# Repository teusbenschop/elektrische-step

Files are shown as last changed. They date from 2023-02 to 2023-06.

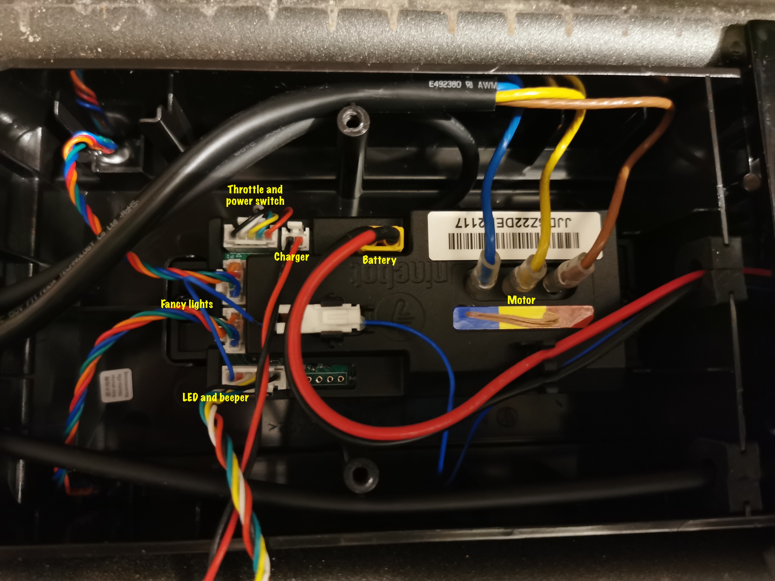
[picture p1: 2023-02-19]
Remarks/Controller-wiring.jpg

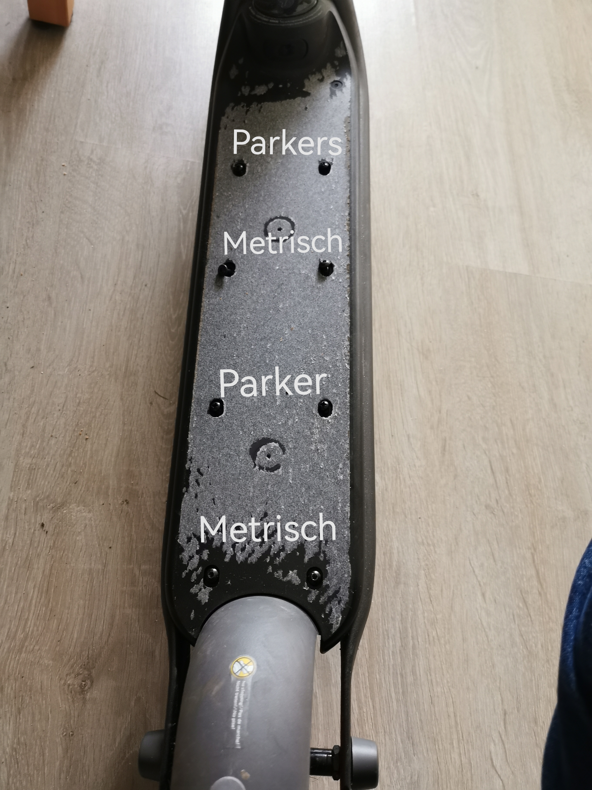
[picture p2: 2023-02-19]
Remarks/Zing C20 foot rest screws.jpg

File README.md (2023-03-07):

# Legale elektrische step

Ideeën en schemas en code voor een elektrische step die legaal is binnen Nederland.

Op de [website van de rijksoverheid.nl staat waaraan een elektrische step moet voldoen om legaal de openbare weg op te kunnen](https://www.rijksoverheid.nl/onderwerpen/voertuigen-op-de-weg/e-step-met-trapondersteuning).

Dit is een samenvatting van het artikel (gecontroleerd maart 2023):

---

Wat is een e-step met trapondersteuning? 
* U stept zelf op deze e-step. 
* Door de hulpmotor gaat u harder vooruit. 
* Maar niet harder dan 25 kilometer per uur.
* De hulpmotor heeft een vermogen van maximaal 250 Watt.

Regels voor gebruik e-step met trapondersteuning.
Voor deze e-step gelden dezelfde regels als voor een elektrische fiets. U hoeft bijvoorbeeld geen rijbewijs te hebben.

Uitrusting die een e-step met trapondersteuning moet hebben:
Een e-step met trapondersteuning heeft:
* een stuur;
* verlichting; 
* rode en witte/gele reflectoren.

Let op! Sommige e-steps hebben een gashendel. Deze werkt niet. Werkt de gashendel wel? Dan is uw e-step een bijzondere bromfiets.

---

Einde samenvatting.

Op de [website van de politieacademie.nl staat ongeveer hetzelfde](https://webapps.politieacademie.nl/bijzondere-bromfiets/53484).

Om een bestaande elektrische step legaal te maken is er het idee om de step te voorzien van detectoren die detecteren als de bestuurder van de step een stepbeweging maakt door met het been af te zetten tijdens het steppen. Dit idee is vorm te geven door lichtbronnen te monteren aan de voetenplank van de step, plus detectoren om de reflectie van dit licht op de voet, die afzet, te detecteren. Dit patroon van reflectie kan dan in een computertje ingevoerd worden, en dat computertje kan dan de motor van de step uitschakelen als er geen beweging van de bestuurder gedetecteerd wordt gedurende een aantal seconden.

De lichtbronnen en lichtdetectoren worden dan gemonteerd op de juiste plaats van de voetenplank waar die het beste de beweging van het been kan detecteren als de bestuurder met de voet afzet.

Als de step nog een gashendel heeft, dan mag die gashendel niet werken.
De meest eenvoudige oplossing is om de gashendel gewoon te verwijderen.
Daarnaast is het als optie mogelijk om een remhendel van bijvoorbeeld de Xiaomi Mi M365 te monteren op de plaats waar de gashendel zat. Die remhendel kan dan fungeren als dodemansknop. Zodra de dodemanshendel ingeknepen wordt, dan wordt de motor toegelaten eventueel aan te gaan als aan alle voorwaarden wordt voldaan. Zodra de dodemanshendel losgelaten wordt, dan schakelt de motor in alle gevallen direct uit.

Hier in deze repository staan een aantal bestanden die de elektonische schakeling weergeven, plus de programmatuur, dat bovenstaand idee vormgeeft.

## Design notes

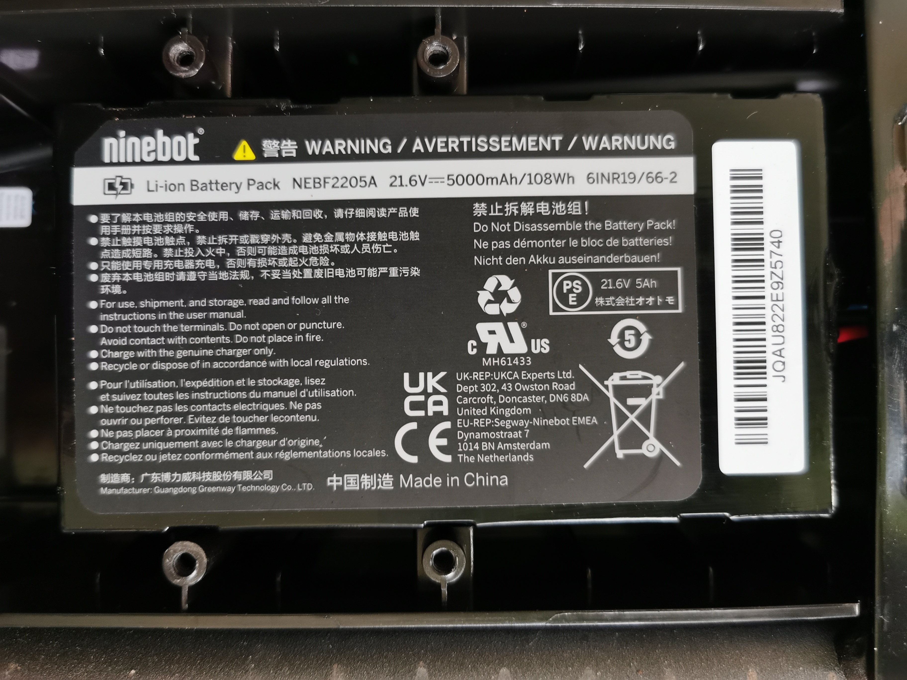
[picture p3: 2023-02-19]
Remarks/Zing-C20-battery.jpg

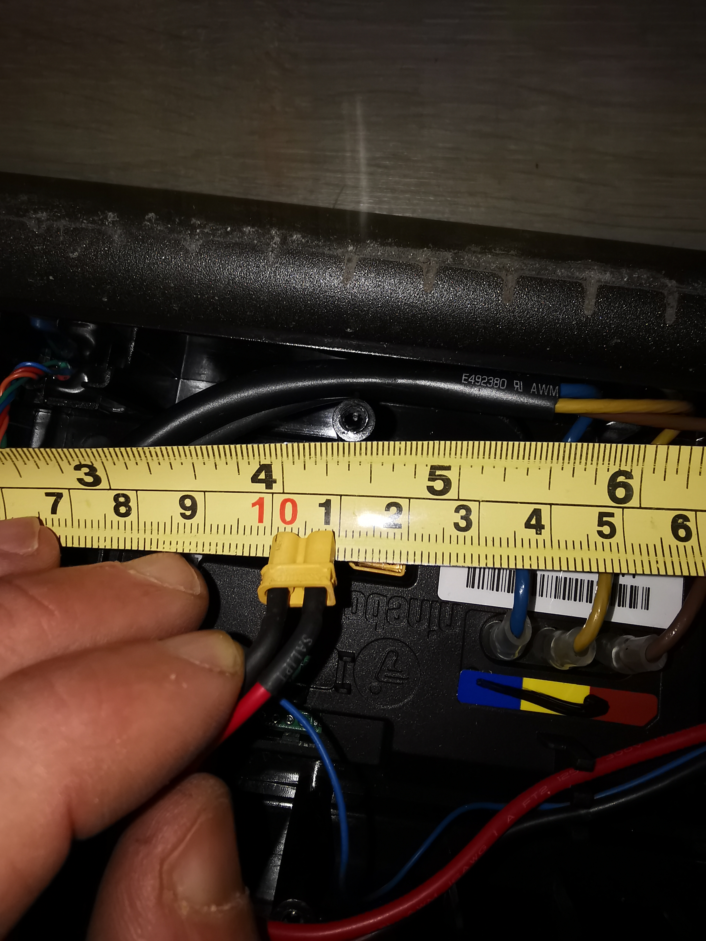
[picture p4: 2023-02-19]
Remarks/XT30-battery-connector.jpg

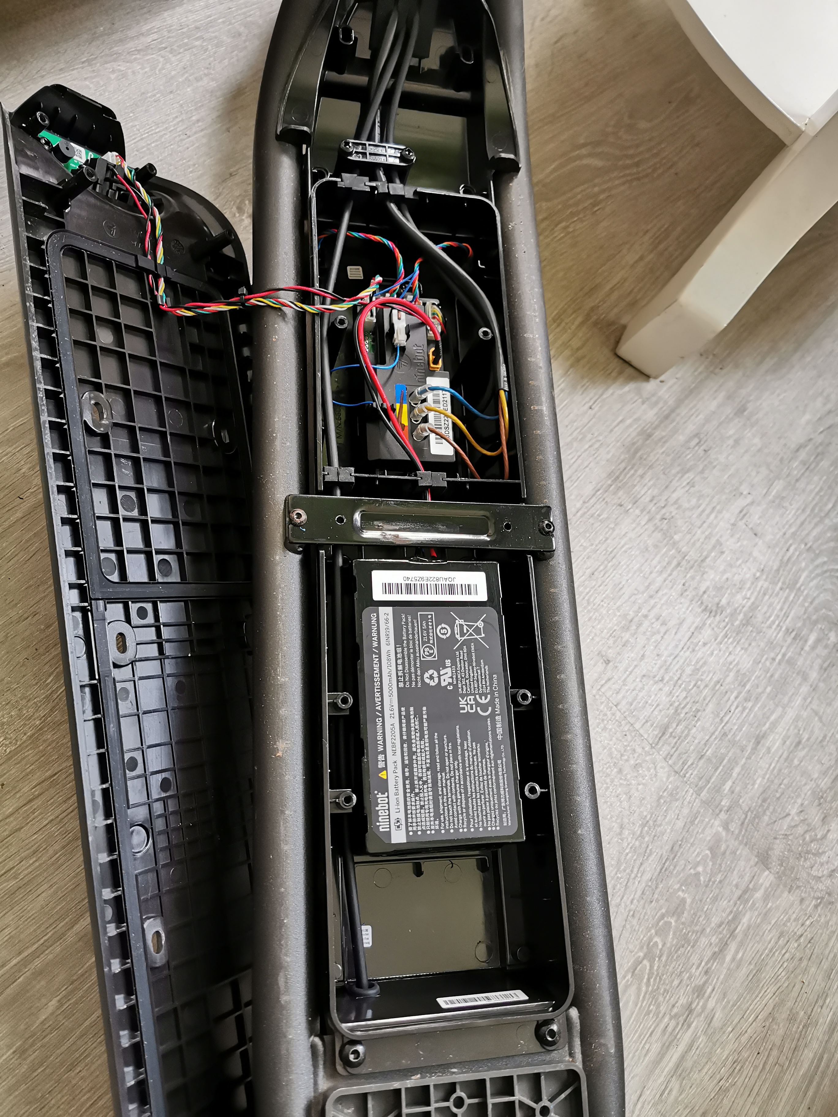
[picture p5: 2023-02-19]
Remarks/Zing C20 bottom box.jpg

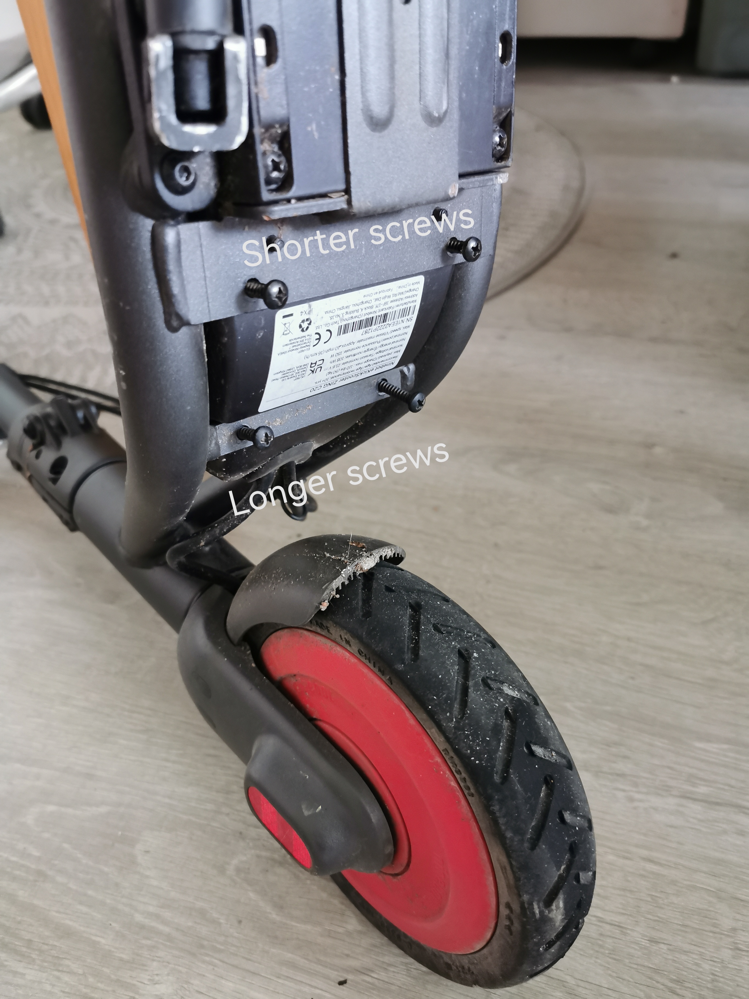
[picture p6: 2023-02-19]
Remarks/Zing C20 bottom screws.jpg

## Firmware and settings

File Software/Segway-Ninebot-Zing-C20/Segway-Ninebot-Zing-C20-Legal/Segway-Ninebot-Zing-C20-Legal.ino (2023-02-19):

// Segway Ninebot Zing C20 Legalizer Software for the Netherlands.


constexpr bool debug {true};
//constexpr bool debug {false};

#include <millisDelay.h>

bool flash_led_on {false};
millisDelay flash_led_delay {};

millisDelay sensor_timer {};

constexpr int photo_diodes_sensitivity {15};

constexpr int photo_diodes_noise_reducing_read_count {10};

constexpr int left_photo_diode_pin {A0};
int left_photo_diode_value {0};
int previous_left_photo_diode_value {0};

constexpr int right_photo_diode_pin {A5};
int right_photo_diode_value {0};
int previous_right_photo_diode_value {0};

constexpr int throttle_input_pin {A2};
int throttle_input_value {0};
// The analogWrite (pin, val) function is applicable to PWM pins (D3, D5, D6, D9, D10, and D11 in Arduino Nano).
// But analogWrite is no longer used on this pin. The scooter motor was stuttering too much.
constexpr int throttle_relay_pin {A1};

// The pin and timer to control the beeper.
constexpr int beeper_pin {8};
millisDelay beeper_timer {};

// The timer to enable the motor.
millisDelay motor_timer {};
// The motor will remain on for n seconds after the last leg movement detection or other trigger.
constexpr int motor_remain_on_seconds {8};
// The number of seconds that the motor-on is timing out.
int motor_timeout_seconds_counter {0};

// The setup function runs once when you press reset or power the board.
void setup () 
{

  // Initialize the serial port for monitoring in debugging mode.
  if (debug) {
    Serial.begin (115200);
    Serial.println ();
    Serial.println ("Segway Ninebot Zing C20 Legalizing Software for the Netherlands version 003");
  }

  // Initialize digital pin LED_BUILTIN as an output.
  // Most Arduinos have an on-board LED you can control. 
  // On the UNO, MEGA and ZERO it is attached to digital pin 13, on MKR1000 on pin 6. 
  // LED_BUILTIN is set to the correct LED pin independent of which board is used.
  // If you want to know what pin the on-board LED is connected to on your Arduino model, 
  // check the Technical Specs of your board at:
  // https://www.arduino.cc/en/Main/Products
  pinMode (LED_BUILTIN, OUTPUT);

  // Initialize the ADC (analog-digital converter).
  // https://reference.arduino.cc/reference/en/language/functions/analog-io/analogreference/
  // https://forum.arduino.cc/t/arduino-nano-undocumented-feature-analogreference-0/362161
  // Be careful with this, as incorrect settings can damage the microcontroller.
  // If the analog reference is not set to "external" but an external voltage is applied to the "ref" pin,
  // this can damage the MCU.
  //analogReference (EXTERNAL);
  
  // Initialize the sensor input pins.
  pinMode (left_photo_diode_pin, INPUT);
  pinMode (right_photo_diode_pin, INPUT);

  // Initialize the throttle input pin.
  pinMode (throttle_input_pin, INPUT);
  // Set the throttle output PWM frequency as high as possible.
  // https://www.etechnophiles.com/how-to-change-the-pwm-frequency-of-arduino-nano/
  // TCCR1B = TCCR1B & B11111000 | B00000001;
  // Initialize the throttle output pin.
  pinMode (throttle_relay_pin, OUTPUT);
  // Initialize the output with some value to avoid errors and red flashing LED of the Ninebot controller,
  // as it initially detects too low an input Voltage on the throttle input.
  // analogWrite (throttle_output_pin, 50);

  // The beeper pin.
  pinMode (beeper_pin, OUTPUT);
  
  // Start the LED flash timer with nnn milliseconds.
  // This is the period between toggling the LED on or off.
  flash_led_delay.start(500);

  // Start the timer for reading the PIR motion sensor and the IR photo diodes every nn milliseconds.
  sensor_timer.start (50);

  // The motor timer will do a cycle every second for doing the housekeeping.
  motor_timer.start (1000);
}


// The loop function runs over and over again forever.
void loop () 
{

  // Handle LED flash timeout.
  if (flash_led_delay.justFinished()) {
    // Repeat the timer.
    flash_led_delay.repeat();
    // Toggle the LED-on flag.
    flash_led_on = !flash_led_on;
    // Turn the LED on or off.
    digitalWrite (LED_BUILTIN, flash_led_on ? HIGH : LOW);
    //digitalWrite (beeper_pin, flash_led_on ? HIGH : LOW);
    //digitalWrite (throttle_relay_pin, flash_led_on ? HIGH : LOW);
    
    // Optionally read the analog input from the photodiode and write it to the serial terminal.
    if (debug) {
      int value {0};
      Serial.print ("left ");
      Serial.print (left_photo_diode_value);
      Serial.print (" right ");
      Serial.print (right_photo_diode_value);
      Serial.print (" throttle ");
      Serial.print (throttle_input_value);
      Serial.print (" timer ");
      Serial.print (motor_timeout_seconds_counter);
      Serial.println ("");
    }
  }

  // Handle the timer to read the sensors.
  if (sensor_timer.justFinished()) {
    sensor_timer.repeat();

    // Read the analog input of the left and right photo diode multiple times to reduce noise.
    left_photo_diode_value = 0;
    right_photo_diode_value = 0;
    for (int i {0}; i < photo_diodes_noise_reducing_read_count; i++) {
      left_photo_diode_value += analogRead(left_photo_diode_pin);
      right_photo_diode_value += analogRead(right_photo_diode_pin);
    }
    left_photo_diode_value /= photo_diodes_noise_reducing_read_count;
    right_photo_diode_value /= photo_diodes_noise_reducing_read_count;

    bool left_sensor_on = (left_photo_diode_value < previous_left_photo_diode_value - photo_diodes_sensitivity);
    previous_left_photo_diode_value = left_photo_diode_value;
    if (left_sensor_on) {
      beep (1);
      kick_motor_timer (motor_remain_on_seconds);
    }

    bool right_sensor_on = (right_photo_diode_value < previous_right_photo_diode_value - photo_diodes_sensitivity);
    previous_right_photo_diode_value = right_photo_diode_value;
    if (right_sensor_on) {
      beep (1);
      kick_motor_timer (motor_remain_on_seconds);
    }

    throttle_input_value = analogRead (throttle_input_pin);
    // The analogRead() values go from 0 to 1023, analogWrite() values from 0 to 255, so divide by 4 (in theory).
    // There is a 2kΩ resistor from the PWM output, and a 100µF capacitor to the ground, 
    // and then this goes to the throttle input of the Ninebot controller.
    // The Ninebot controller draws a bit of current too.
    // So by trial and error, the throttle division factor is determined as below instead of being 4.
    //constexpr float throttle_division_factor {3.55};
    //analogWrite (throttle_output_pin, throttle_input_value / throttle_division_factor);
    // Just now do it such that if the throttle is closed three times, a new period of time is given to the motor enable.
    if (throttle_input_value < 200) {
      kick_motor_timer ((motor_remain_on_seconds / 3) + 1);
    }
  }  

  if (beeper_timer.justFinished()) {
    digitalWrite (beeper_pin, LOW);
  }

  if (motor_timer.justFinished ()) {
    // Repeat the timer.
    motor_timer.repeat();
    // Increase the timeout counter.
    motor_timeout_seconds_counter++;
    // Check if the motor should be switched off.
    if (motor_timeout_seconds_counter >= motor_remain_on_seconds) {
      digitalWrite (throttle_relay_pin, HIGH);
    }
    
  }

}

void beep (const int milliseconds)
{
  beeper_timer.start (milliseconds);
  digitalWrite (beeper_pin, HIGH);
}


void kick_motor_timer (int value)
{
  motor_timeout_seconds_counter -= value;
  if (motor_timeout_seconds_counter < 0) motor_timeout_seconds_counter = 0;
  if (motor_timeout_seconds_counter == 0) {
    digitalWrite (throttle_relay_pin, LOW);
  }
}

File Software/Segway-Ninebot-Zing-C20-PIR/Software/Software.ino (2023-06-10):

// Segway Ninebot Zing C20 Legalizer Software for the Netherlands.
// It uses a PIR detector to detect the kick movement of the legs.


//constexpr bool debug {true};
constexpr bool debug {false};

// The timer library.
#include <millisDelay.h>
// The library for I2C
#include <Wire.h>
// The MCP 4725 DAC library.
#include <Adafruit_MCP4725.h>

millisDelay flash_led_delay {};

millisDelay sensor_timer {};

constexpr int throttle_input_pin {A0};
int throttle_input_value {0};

// The digital to analog converter.
Adafruit_MCP4725 digital_analog_converter;

// The value where the throttle is fully closed. This was measured in a real configuration.
constexpr int throttle_idle_input {183};
constexpr int throttle_idle_output {727};

// The actual throttle output voltage.
int throttle_output_value {throttle_idle_output};

constexpr int beeper_pin {8};
millisDelay beeper_timer {};

millisDelay motor_timer {};

// The motor will remain on for n seconds after the last leg movement detection or other trigger.
constexpr int motor_remain_on_seconds {8};

// The number of seconds that the motor-on is now timing out.
int motor_timeout_seconds_counter {0};

// PIR sensor.
constexpr int pir_pin {5};


// The setup function runs once when you press reset or power the board.
void setup () 
{
  // Initialize the serial port for monitoring in debugging mode.
  if (debug) {
    Serial.begin (115200);
    Serial.println ();
    Serial.println ("Segway Ninebot Zing C20 Legalizing Software for the Netherlands");
  }

  // Initialize digital pin LED_BUILTIN as an output.
  // Most Arduinos have an on-board LED you can control. 
  // On the UNO, MEGA and ZERO it is attached to digital pin 13, on MKR1000 on pin 6. 
  // LED_BUILTIN is set to the correct LED pin independent of which board is used.
  // If you want to know what pin the on-board LED is connected to on your Arduino model, 
  // check the Technical Specs of your board at:
  // https://www.arduino.cc/en/Main/Products
  pinMode (LED_BUILTIN, OUTPUT);

  // Initialize the throttle input pin.
  pinMode (throttle_input_pin, INPUT);

  // The beeper pin.
  pinMode (beeper_pin, OUTPUT);

  // Begin the I2C communication at these pins:
  // Arduino A4 = SDA (serial data).
  // Arduino A5 = SCL (serial clock).
  Wire.begin();

  // For Adafruit MCP4725A1 the I2C address is 0x62 (default) or 0x63 (ADDR pin tied to VCC).
  digital_analog_converter.begin (0x62);
  
  // Start the LED flash timer with nnn milliseconds.
  // This is the period between toggling the LED on or off.
  flash_led_delay.start(500);

  // Start the timer for reading the PIR motion sensor every nn milliseconds.
  // Note: Another method is to count the pulses and so attach an interrupt to the PIR sensor input pin.
  sensor_timer.start (50);

  // The motor timer will do a cycle every second for doing the housekeeping.
  motor_timer.start (1000);

  // Initialize the PIR pin.
  pinMode (pir_pin, INPUT);
}


// The loop function runs over and over again forever.
void loop () 
{

  // Handle LED flash timeout.
  if (flash_led_delay.justFinished()) {
    // Repeat the timer.
    flash_led_delay.repeat();
    // Toggle the LED.
    toggle_built_in_led ();
    
    // Optionally read the analog input from the photodiode and write it to the serial terminal.
    if (debug) {
      Serial.print (" throttle input ");
      Serial.print (throttle_input_value);
      Serial.print (" output ");
      Serial.print (throttle_output_value);
      Serial.print (" timer ");
      Serial.print (motor_timeout_seconds_counter);
      Serial.println ("");
    }
  }

  // Handle the timer to read the sensors.
  if (sensor_timer.justFinished()) {
    sensor_timer.repeat();

    bool pir_state = digitalRead (pir_pin);
    if (pir_state) {
      toggle_built_in_led ();
      beep (1);
      kick_motor_timer (motor_remain_on_seconds);
    }

    // The analogRead() value is 10 bits wide so goes from 0 to 1023.
    throttle_input_value = analogRead (throttle_input_pin);

    // The DAC is 12 bits, to its input value can vary between 0 and 4095.
    // So multiply the input value by 4 then.
    int throttle_value_12_bits = 4 * throttle_input_value;

    // Check if the motor should be switched off.
    if (motor_timeout_seconds_counter >= motor_remain_on_seconds) {
      throttle_value_12_bits = throttle_idle_output;
    }

    if (throttle_value_12_bits != throttle_output_value) {
      // Normally the value to change the throttle output with is 10% of the absolute difference.
      // But if the difference is larger, then the throttle output immediately jumps to the final value.
      int difference = abs (throttle_value_12_bits - throttle_output_value);
      int change = difference / 10;
      if (difference > 1000) change = difference;
      // Change the throttle output up or down.
      if (throttle_value_12_bits < throttle_output_value) throttle_output_value -= change;
      if (throttle_value_12_bits > throttle_output_value) throttle_output_value += change;
      digital_analog_converter.setVoltage (throttle_output_value, false);
    }

    // If the throttle is released, the motor time-out restarts.
    if (throttle_input_value < (throttle_idle_input * 1.1)) {
      kick_motor_timer ((motor_remain_on_seconds / 3) + 1);
    }
  }  

  if (beeper_timer.justFinished()) {
    digitalWrite (beeper_pin, LOW);
  }

  if (motor_timer.justFinished ()) {
    // Repeat the timer.
    motor_timer.repeat();
    // Increase the timeout counter.
    motor_timeout_seconds_counter++;
  }

}

void beep (const int milliseconds)
{
  beeper_timer.start (milliseconds);
  digitalWrite (beeper_pin, HIGH);
}


void kick_motor_timer (int value)
{
  motor_timeout_seconds_counter -= value;
  if (motor_timeout_seconds_counter < 0) motor_timeout_seconds_counter = 0;
}


void toggle_built_in_led ()
{
  static bool led_on {false};
  led_on = !led_on;
  digitalWrite (LED_BUILTIN, led_on ? HIGH : LOW);
}

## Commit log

2023-02-19 Segway Ninebot Zing C20 ombouw
    [Schematic001.kicad_pcb, Schematic001.kicad_sch]
2023-03-07 Update on throttle and brake lever
